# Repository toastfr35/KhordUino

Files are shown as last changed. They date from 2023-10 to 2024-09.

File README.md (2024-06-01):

<p align="center">
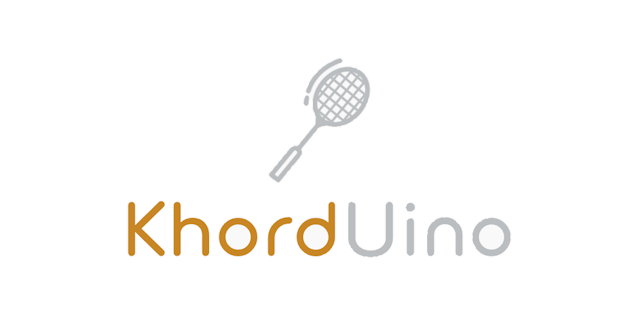
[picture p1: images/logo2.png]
  
</p>

# KhordUino (3D Printed Electronic Badminton Stringer)

Welcome to the KhordUino project, a 3D Printed Electronic Badminton Stringer. 

https://github.com/toastfr35/KhordUino/assets/11369231/e21abeb8-c3cd-45fe-b324-fbe94404d06a

## Mechanical design

A stringing machine usually comprises a stable frame, clamps to hold strings in place and a tensioning system to tighten strings. 
Electronic models have control panels for precision. 

The KhordUino design is quite different from most metal frame stringing machines. In these machines (see below), the rotating joint for the frame is quite far from the tensioning plane.

<p align="center">
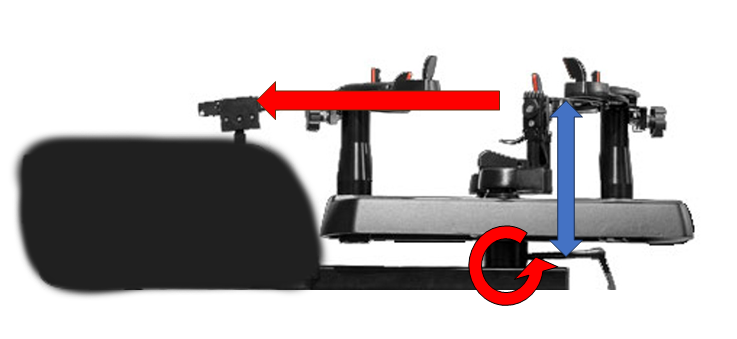
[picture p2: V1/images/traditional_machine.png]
  
</p>

In order to not require many metal components the rotating element (holding the racket) and the part pulling 
on the strings should be aligned as much as possible to minimise the moment (blue arrow).
This is achieved by keeping the machine quite flat (which is also great for storage).

<p align="center">
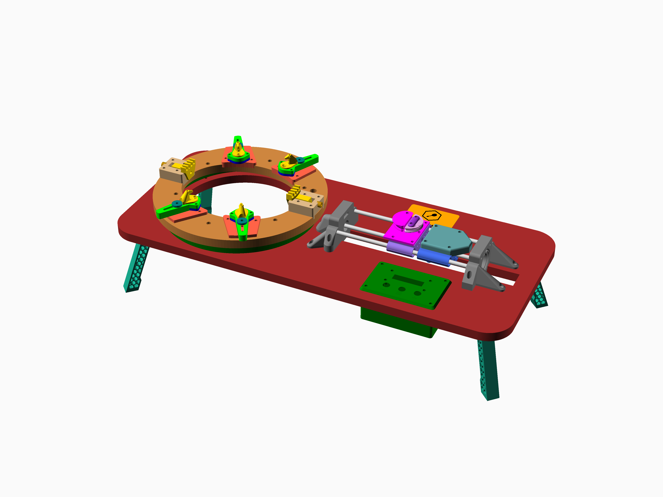
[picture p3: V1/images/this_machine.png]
  
</p>

<p align="center">
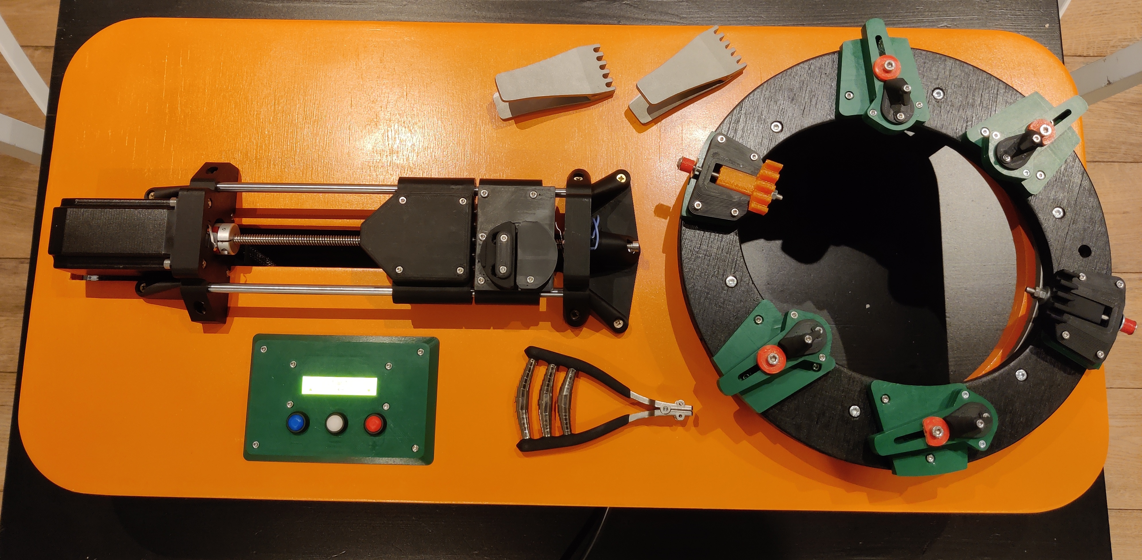
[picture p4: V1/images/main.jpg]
  
</p>

The rotation joint is kept very close to the racket face. This can only be achieved by using a large bearing "around" the racket rather than underneath it.
As the rotating joint and the tensioning part of the machine are almost in the same plane the resulting Moment is greatly reduced.

## BOM

[KhordUino Bill of Material (spreadsheet)](https://docs.google.com/spreadsheets/d/1VggcFAZ6FdfzaC9WXAd_AR7_Q7eQJJpP21XG0TGiltw/edit?usp=sharing)

## Documentation

The [Assembly Manual](V1/KhordUino_Manual.pdf) provides a step-by-step guide to print and assemble your own KhordUino.

## License

KhordUino © 2023 by Antoine Colin is licensed under CC BY-NC-SA 4.0

## Versions

KhordUino V1 is available now.

KhordUino V2 is a work in progress and will be made available once fully tested.

## Videos

[Calibration procedure](https://youtu.be/ICjtoKouB5M)

[Using the string puller](https://youtu.be/xCwdWevW81s)

## Updates:

- V1.1 (2024-05-27).  New firmware with easier calibration procedure.

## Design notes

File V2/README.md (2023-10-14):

# Khorduino V2

## Goals

- Lower BOM cost.
- Fewer different parts to assemble.
- Use standard (still cheap) load cell.
- Easier wiring.
- Lighter, smaller.
- Simplified stringing operation.

## Difference with V1

- More compact (base board length and width reduced to minimum).
- Fewer (larger) 3D printed parts.
- Fewer bolts and nuts
- Fewer different sizes of bolts and nuts.
- No linear bearings.
- Different load cell (and placement of).
- Battery powered (via adapters, e.g. Ryobi 18V battery).
- Single limit switch (other limit enforced in software).
- A single 3 positions switch for stringing operation (pull, idle, release).
- No LCD. Instead Bluetooth + Android/IOS App for settings.
- Slightly longer legs for a bit more clearance.
- Buzzer to indicate desired tension is reached.

## What will be the same

The general design remains the same.

- NEMA23 stepper motor (required for the needed torque).
- Large bearing to access the racquet face from top and bottom.

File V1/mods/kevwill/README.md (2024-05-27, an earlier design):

[kevwill Khorduino Remix](https://www.thingiverse.com/thing:6637585)

#### Summary

I remixed a few parts from toastfr35's KhordUino badminton stringing machine to fit my specific needs:

1.  PSU Box 1 (PSU_Box_1) and Box 2 (PSU_Box_2): I added a cutout for a C13 socket and switch, and modified the vent holes to fit my PSU.
2.  Control Panel Body (CP_body): I modified the external holes to accommodate my wiring and changed the interior mounting posts to fit the Arduino Nano breakout board, buck converter, and terminal block that I used in my build.
3.  Working disc base segment (WD_base_segment): I combined two working disc base segments into one piece to make assembly easier.
4.  Tool drawer (Drawer) and rail (Drawer_rail): I modified the drawer and rail so that the drawer latches closed, preventing the drawer from sliding open and spilling tools during transport.

Here are the specific parts I ordered that fit these modifications:

[https://www.amazon.com/gp/product/B06XK2ZNKC/ref=ppx_yo_dt_b_search_asin_title?ie=UTF8&psc=1](https://www.amazon.com/gp/product/B06XK2ZNKC/ref=ppx_yo_dt_b_search_asin_title?ie=UTF8&psc=1)  
[https://www.amazon.com/gp/product/B09LGX9MQX/ref=ppx_yo_dt_b_search_asin_title?ie=UTF8&psc=1](https://www.amazon.com/gp/product/B09LGX9MQX/ref=ppx_yo_dt_b_search_asin_title?ie=UTF8&psc=1)  
[https://www.amazon.com/gp/product/B0BF9H89HD/ref=ppx_yo_dt_b_search_asin_title?ie=UTF8&psc=1](https://www.amazon.com/gp/product/B0BF9H89HD/ref=ppx_yo_dt_b_search_asin_title?ie=UTF8&psc=1)  
[https://www.amazon.com/gp/product/B0BXKZQB1H/ref=ppx_yo_dt_b_search_asin_title?ie=UTF8&psc=1](https://www.amazon.com/gp/product/B0BXKZQB1H/ref=ppx_yo_dt_b_search_asin_title?ie=UTF8&psc=1)  
[https://www.amazon.com/dp/B0BMTKGCM6?psc=1&ref=ppx_yo2ov_dt_b_product_details](https://www.amazon.com/dp/B0BMTKGCM6?psc=1&ref=ppx_yo2ov_dt_b_product_details)  
[https://www.amazon.com/gp/product/B085CGGH4W/ref=ppx_yo_dt_b_search_asin_title?ie=UTF8&psc=1](https://www.amazon.com/gp/product/B085CGGH4W/ref=ppx_yo_dt_b_search_asin_title?ie=UTF8&psc=1)

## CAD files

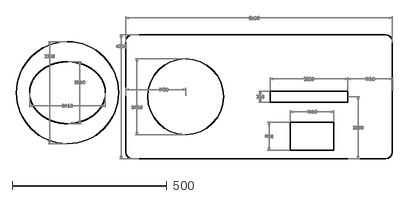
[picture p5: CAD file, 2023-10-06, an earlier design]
V1/plywood_template/board.dxf
1215.3 x 459.3

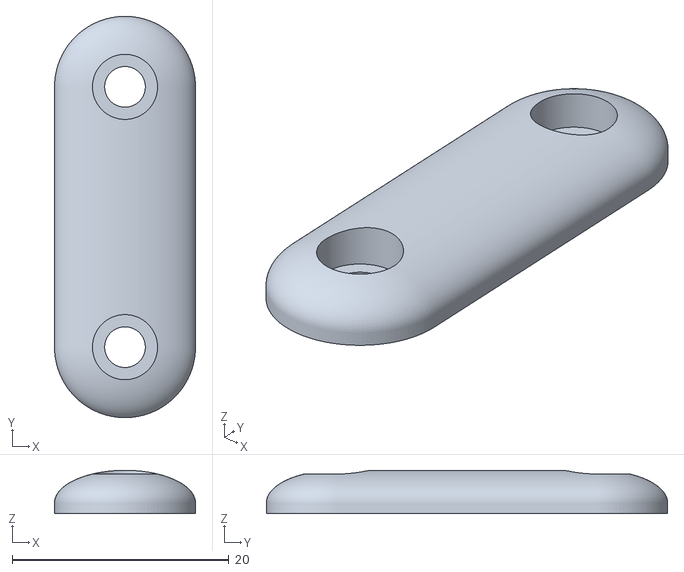
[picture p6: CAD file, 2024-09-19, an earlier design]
V1/STLs/GS_mobile_jaw_retainer.stl
13.0 x 37.0 x 4.00

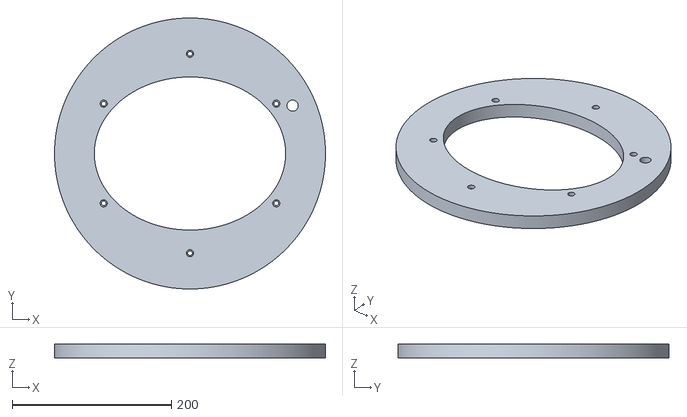
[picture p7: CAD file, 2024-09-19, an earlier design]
V1/STLs/WD.stl
340.0 x 340.0 x 18.0

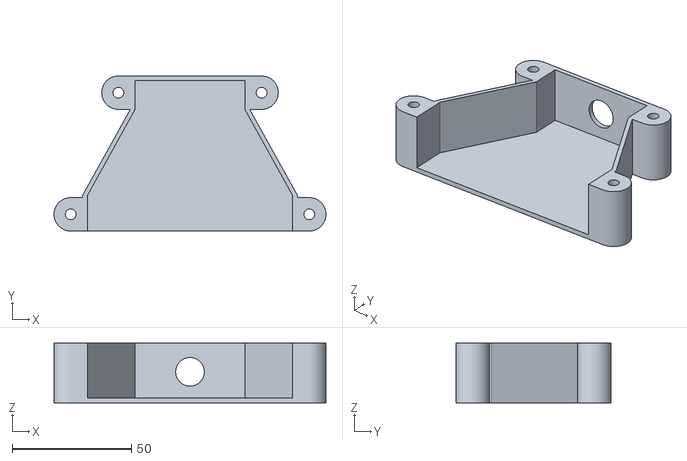
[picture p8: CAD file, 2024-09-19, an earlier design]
V1/STLs/BB_stepper_driver_cover.stl
114.0 x 65.0 x 25.0

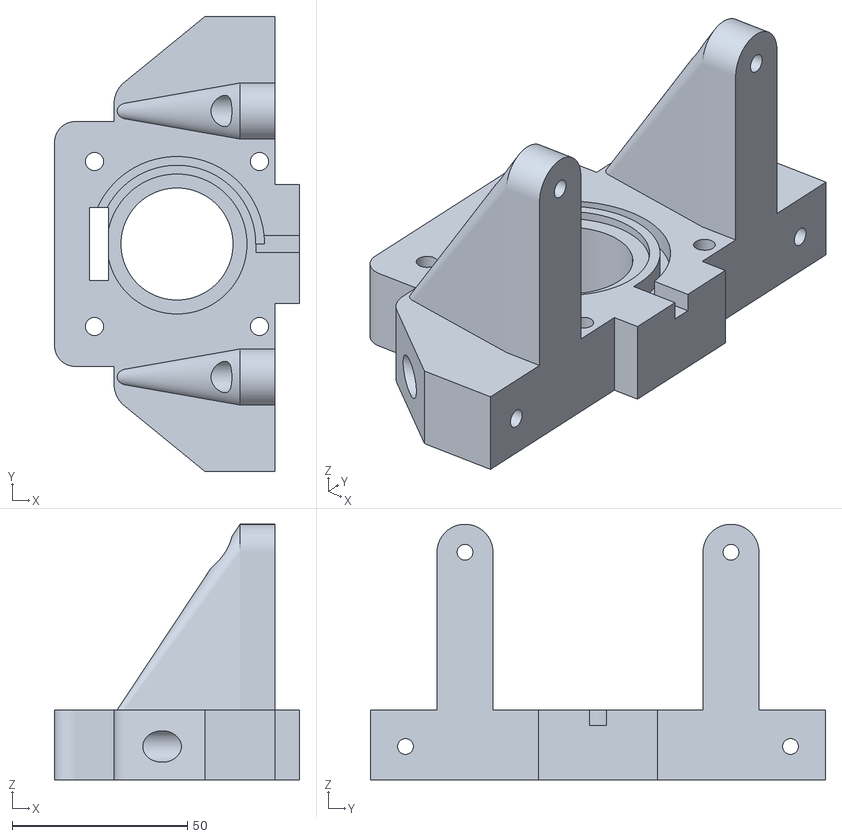
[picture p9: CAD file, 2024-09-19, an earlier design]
V1/STLs/MB.stl
70.0 x 130.0 x 73.0

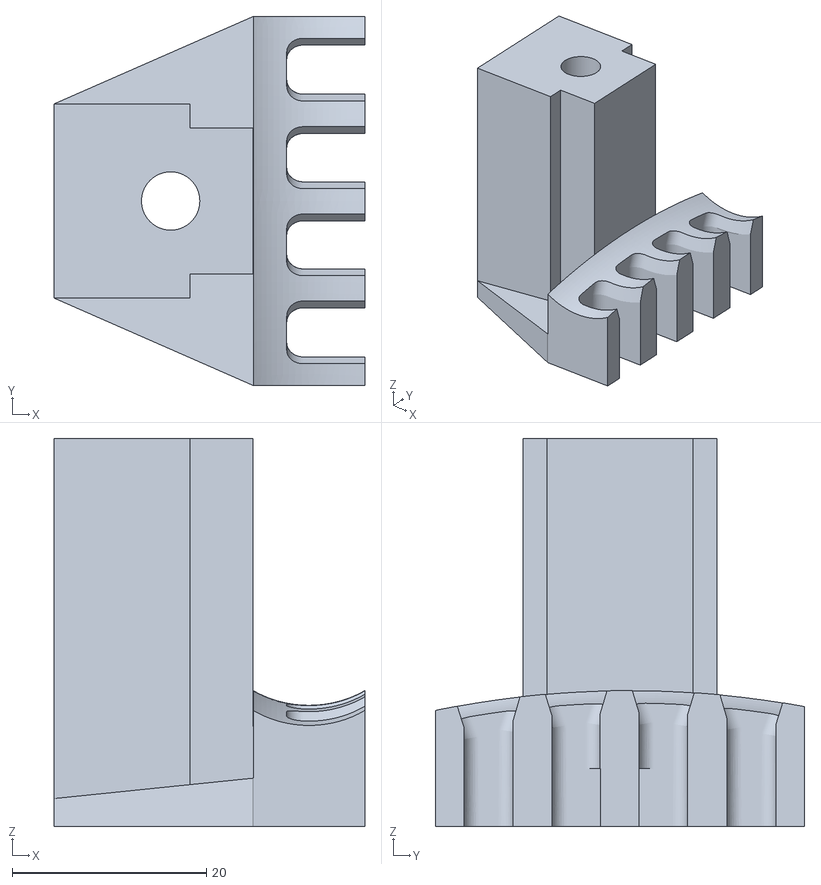
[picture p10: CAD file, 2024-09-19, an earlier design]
V1/STLs/THS_gripper.stl
32.0 x 38.0 x 40.0

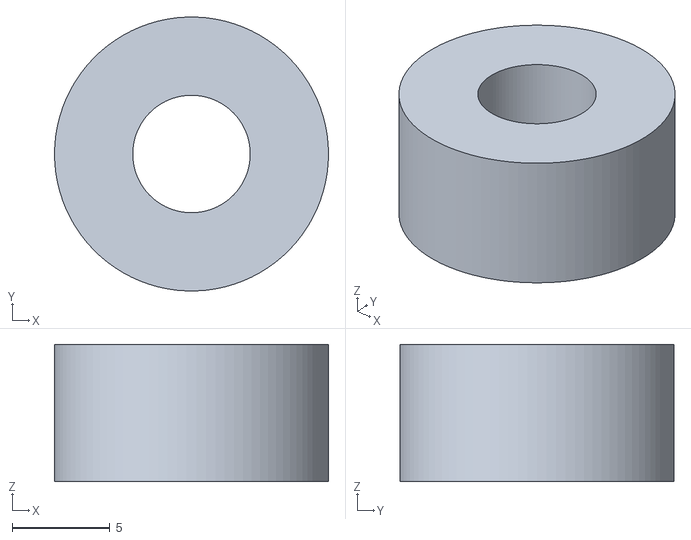
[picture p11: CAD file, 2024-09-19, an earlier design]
V1/STLs/WD_spacer.stl
14.0 x 14.0 x 7.00

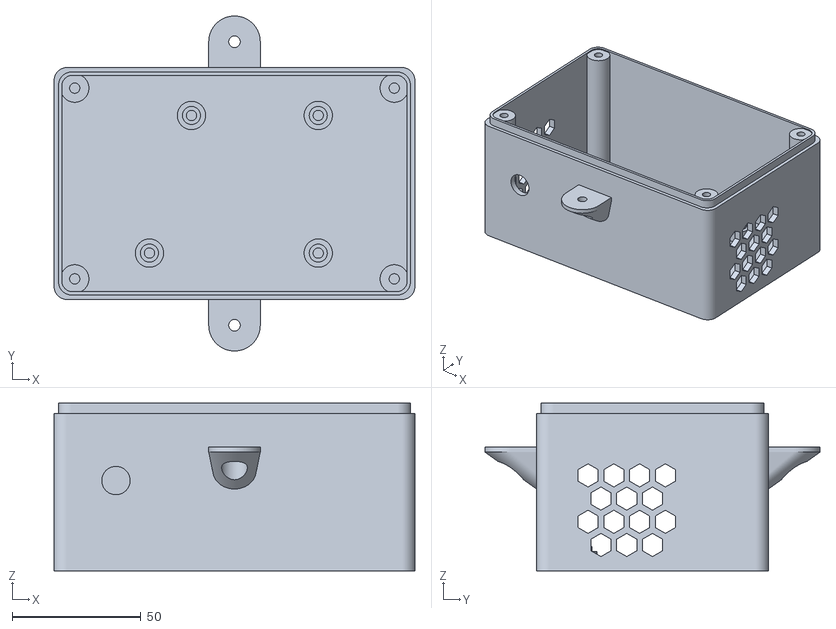
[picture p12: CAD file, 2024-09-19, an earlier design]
V1/STLs/CP_body.stl
140.0 x 130.0 x 65.0

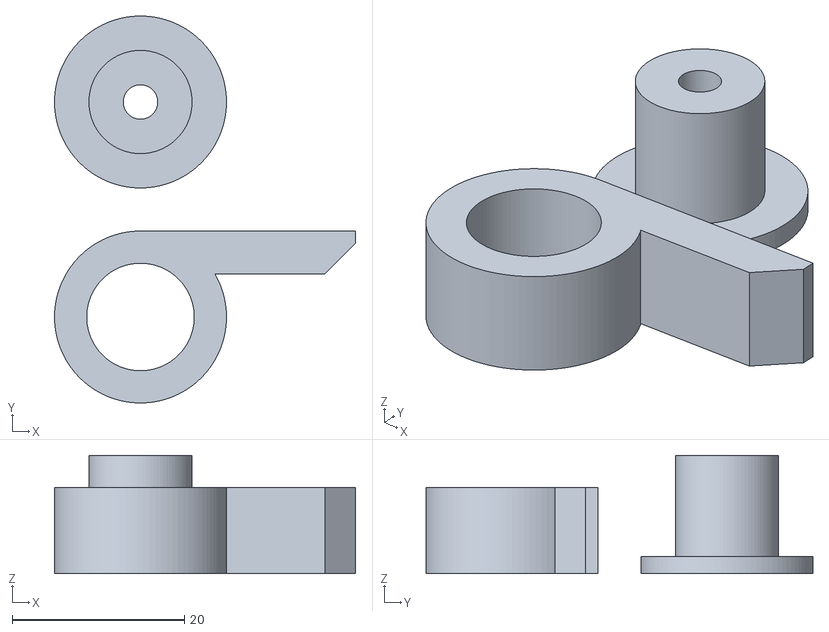
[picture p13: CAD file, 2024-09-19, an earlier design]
V1/STLs/Drawer_latch.stl
35.0 x 45.0 x 13.8

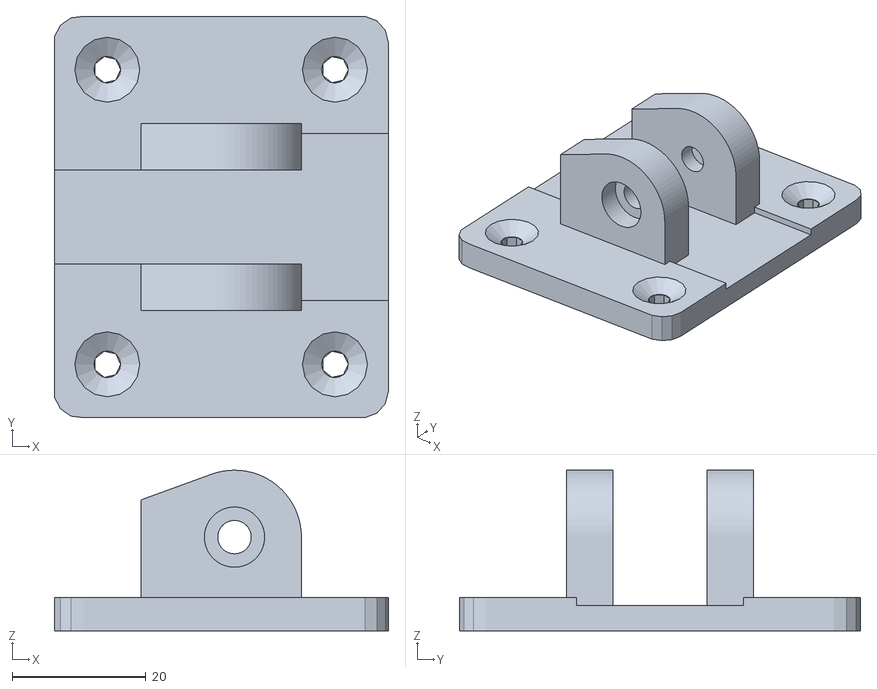
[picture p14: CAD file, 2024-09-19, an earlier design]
V1/STLs/BB_leg_hinge.stl
49.9 x 59.9 x 24.0

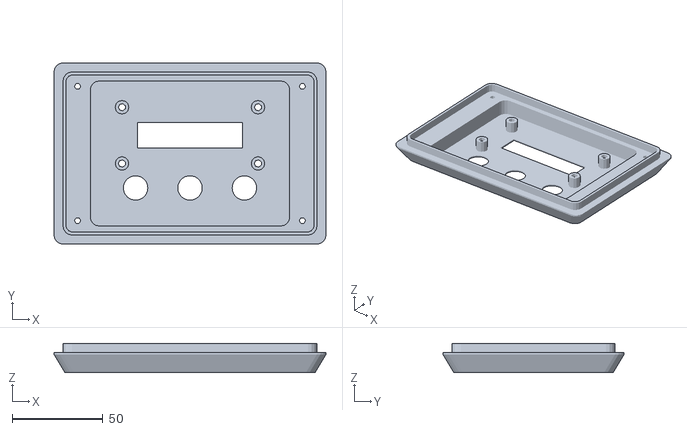
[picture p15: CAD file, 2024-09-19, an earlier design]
V1/STLs/CP_cover.stl
150.0 x 100.0 x 16.0

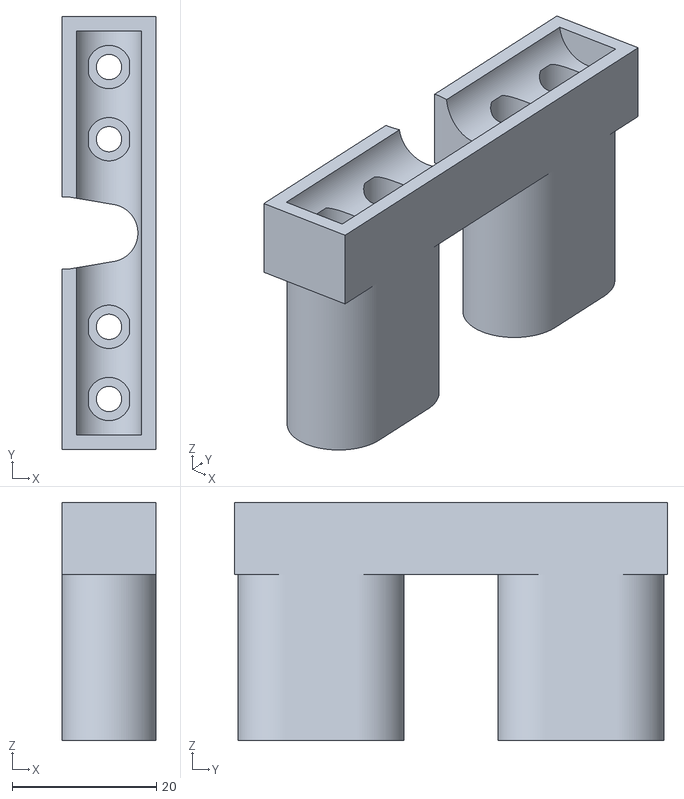
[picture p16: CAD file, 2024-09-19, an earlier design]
V1/STLs/GS_springs_housing.stl
13.0 x 60.0 x 33.0

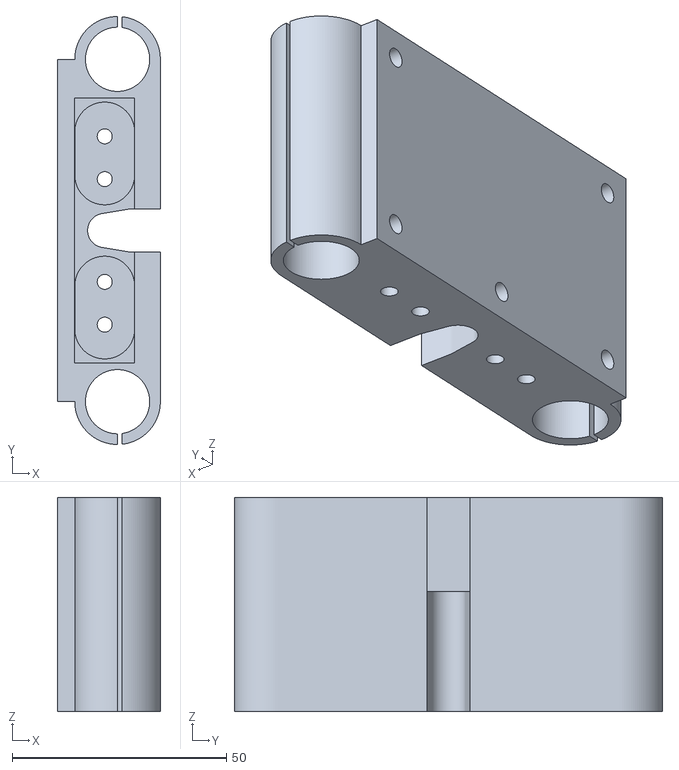
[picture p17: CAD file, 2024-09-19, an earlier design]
V1/STLs/GS_body.stl
24.0 x 100.0 x 50.0

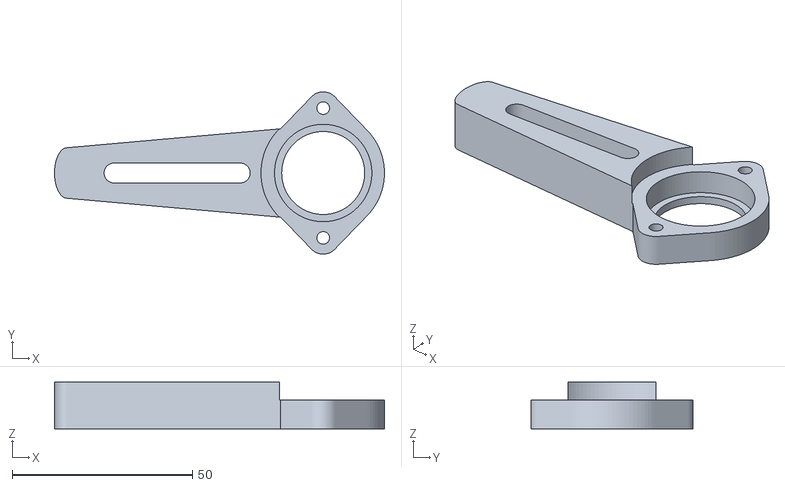
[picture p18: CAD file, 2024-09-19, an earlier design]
V1/STLs/RFS_arm.stl
91.5 x 45.0 x 13.0

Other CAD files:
V1/STLs/BB.stl
V1/STLs/Drawer_rail.stl
V1/STLs/EB.stl
V1/STLs/THS_spacer.stl
V1/SCADs/BB_leg.scad
V1/SCADs/BB_leg_hinge.scad
V1/SCADs/BB_stepper_driver_bracket.scad
V1/SCADs/BB_stepper_driver_cover.scad
V1/SCADs/BB.scad
V1/SCADs/BB_cable_retainers.scad
V1/SCADs/CP_body.scad
V1/SCADs/CP_cover.scad
V1/SCADs/Drawer.scad
V1/SCADs/Drawer_latch.scad
V1/SCADs/Drawer_rail.scad
V1/SCADs/EB.scad
V1/SCADs/GS_body.scad
V1/SCADs/GS_fixed_jaw.scad
V1/SCADs/GS_mobile_jaw.scad
V1/SCADs/GS_mobile_jaw_retainer.scad
V1/SCADs/GS_springs_housing.scad
V1/SCADs/MB.scad
V1/SCADs/PSU_box_1.scad
V1/SCADs/PSU_box_2.scad
V1/SCADs/RFS_arm.scad
V1/SCADs/RFS_base.scad
V1/SCADs/RFS_bottom_cap.scad
V1/SCADs/RFS_gripper.scad
V1/SCADs/RFS_rotating_disc.scad
V1/SCADs/RFS_washer.scad
V1/SCADs/THS_base.scad
V1/SCADs/THS_body.scad
V1/SCADs/THS_gripper.scad
V1/SCADs/THS_spacer.scad
V1/SCADs/TS_body.scad
V1/SCADs/TS_top.scad
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

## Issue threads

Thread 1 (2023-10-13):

CAD files

drnedm, 2023-10-13:
Hi,
thanks so much for sharing this project! I'm building the tensioner part to use it on an old existing drop-weight machine. In order to make an adapter plate, it would be super helpful to not only have the STLs but also an assembled CAD file, STEP format or similar.
Would you be willing to share that as well?

Cheers,
D

toastfr35, 2023-10-13:
Hi, the source is all OpenSCAD but the code is quite a mess at the moment. Let me know which STLs you need and I'll clean these first and put them online.

drnedm, 2023-10-13:
Great, thanks again!

openSCAD is also perfectly fine, I'd be fine with messy openSCAD as well.

For me personally the whole tensioner assembly is relevant, while the rotating racket mount part is not.

drnedm, 2023-10-13:
So from the manual I think that would be

EB.stl
MB.stl
TS_body.stl
TS_top.stl
GS_body.stl
GS_springs_housing.stl
GS_fixed_jaw.stl
GS_mobile_jaw.stl
GS_mobile_jaw_retainer.stl

toastfr35, 2023-10-13:
Here they are in the SCADs directory.  Not super-clean but I'll improve this later.

Closed 2023-10-13.

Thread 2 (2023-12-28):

Load cell and motor firmware

Phyntox, 2023-12-28:
Hi. I have a problem getting the readings from the load cell. I think I connected everithing right.
Also, I have problems running the motor. Nothing seems to happen.

I am using the Arduino UNO. Maybe this is the problem. All the buttons are working.

Could you please share the wiring diagram (more detailed like the DM542 wiring..)

Also it would be nice to have a cancle or back button when you are in the set and pull option.

And a reset button maybe  (Maybe combination of long press of two buttons)?

klwill1192, 2023-12-30:
Can you tell me which luggage scale you bought to get the load cell?  I've bought a couple and neither was the right one for this project.  Thank you.

Phyntox, 2023-12-30:
Any load cell should work, but i thik the problem is that the code is tailored to one type. I'm tearing the code back to the raw reading of the cell and I'll try to "calibrate" the reading to get something useful out

Phyntox, 2023-12-30:
I think i somehow calibrated the load cell inside the code.

Now i just need to see the actual wiring of the DM542. Can someone share a diagram or picture?

klwill1192, 2023-12-31:
I'm still a little ways away from wiring up the badminton stringer, but
here are some pics from another project I designed that also used a DM542
and stepper motor.  You can see how the stepper motor connects to the DM542
here.  If the motor spins the reverse of what you expect, I believe
swapping the two inner or two outer wires will fix the problem.

Here is the original project:  https://imgur.com/gallery/xcwB9ku

[image: IMG_20231230_201622__01.jpg]
[image: IMG_20231230_201440__01.jpg][image: IMG_20231230_201528__01.jpg]

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

klwill1192, 2023-12-31:
> I think i somehow calibrated the load cell inside the code.
>
> Now i just need to see the actual wiring of the DM542. Can someone share a diagram or picture?

I'm still a little ways away from wiring up the badminton stringer, but
here are some pics from another project I designed that also used a DM542
and stepper motor.  You can see how the stepper motor connects to the DM542
here.  If the motor spins the reverse of what you expect, I believe
swapping the two inner or two outer wires will fix the problem.

Here is the original project:  https://imgur.com/gallery/xcwB9ku

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

Phyntox, 2023-12-31:
I did it. i forgot to wire the GNDto EN-. now it works. I need to fine tune the pulling force.

StealthSZN, 2024-01-03:
Hello,

I'm new to the 3d print world, and going to attempt this project. Do you guys have any additional recourses/photos/videos that you could share, and would help me out. Reading over the manual, it would be great to have some videos or pictures to go along as I on not to well versed in these types of projects.

I would appreciate it a ton!

StealthSZN, 2024-01-03:
It would also be great if someone could look over my parts list to make sure everything I am going to order is compatible.

Phyntox, 2024-01-03:
Buy as it is written in BOM. but expect to do some 3d modelling. My cell was different so i had to make an adapter. And then the calibration of the cell.  And steeper driver... just start and learn and solve problems when they occur. Ill try to help as much as i can 😉

StealthSZN, 2024-01-03:
That would be awesome, only questions I have right now is: do i need an Arduino Breakout board? or do I only need the nano?
and can you link me the lazy susan you used? I cant seem to find one online that matches the photos in the manual.

Do you have another place I can message you if I have any questions?

Thanks a ton!

Phyntox, 2024-01-04:
I used arduino Uno. With breakout board. It's easier. And I made some adjustments regarding the main board. I am planning to make ot a bit different so for the concept testing i just 3d printed the bearing and used airsoft balls. It works perfectly (for testing at least)

klwill1192, 2024-01-04:
> So doable without the breakout board or should I just get one to make it easier?

Both.  I am using a Nano with the breakout board.  It's pretty cheap compared to the total cost of the project, so I think the convenience is worth the expense.

Here's the lazy susan I ordered:  https://www.amazon.com/gp/product/B07T2D8D71

You'll end up drilling out all12 holes, so it doesn't matter if some of them don't go all the way through.  The important thing is that this one had 6 each on both the inner and outer circles.

You probably won't find the bearing that matches the instructions.  I've ordered 10 different luggage scales and none of them were the right type.  I've got four more on the way, but I'm not hopeful.  Fortunately Amazon lets me return the ones I'm not going to use.  I'm currently deciding between modifying one of the luggage scale load cells or purchasing a 30 kg S-type tension load sensor and building my own rig.  Antoine said that V2 will use a different load cell.  It would be nice if he'd give us a sneak peak.  I've reached out through GitHub, but haven't gotten a response yet.

I have also modifiect the PSU box to use an intgrated plug/switch/fuse.

Antoine also said that he elongated the legs a bit for V2, so I may do that with V1.

One more item on the shopping list:  a cheap racket to test with.  Not going to start out with one of my nicer ones.

StealthSZN, 2024-01-04:
Luckily i have a cheap racket I can use haha.

Thank you for all the info, I really appreciate it!

This is the load cell I was going to order, curious to know if you guys think it'll work: https://shorturl.at/rCEIX

klwill1192, 2024-01-04:
> This is the load cell I was going to order, curious to know if you guys think it'll work: https://shorturl.at/rCEIX

Whether or not it will work depends on what's inside the case.  The issue isn't so much the load cell as the hardware that connects to the two sides, and whether it can be adapted to connect between  the gripper and tensioner.

I'm seriously thinking about abandoning the cheap luggage scales and redesign the parts to use this:  https://www.amazon.com/dp/B0CPDZ7RS6

StealthSZN, 2024-01-04:
hmm yeah I knew it might be an issue. I was debating to either attempt to build it now, or wait for V2. I'm only about halfway done printing all the parts. I would be of no help trying to redesign the tensioning unit, but if you figure out a better way and would be willing to share, that would be amazing.

Phyntox, 2024-01-04:
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

StealthSZN, 2024-01-04:
Looks awesome, how were you able to get it to work? just changing the code?

Can you convert it into lbs?

Phyntox, 2024-01-04:
`/********************************************************/
/*                  TENSION                             */
/********************************************************/

/*********************************
 * Display the current tension immediately
 *********************************/
void show_tension_now()
{
  lcd.setCursor(0, 0);
  ///////lcd.print(loadcell.read()); // for testing the output measurement
  lcd.print("     " + String(tension_kg / 10) + "." + String(tension_kg % 10) + " kg    ");
}
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
Phyntox, 2024-01-04:
yes, it can be converted to lbs.
you should calibrate the cell anyway so the numerical readout doesnt really matter.
And in the code press ctrl+H and replace the kg for lbs... but in my case I converted lbs to kg.

StealthSZN, 2024-01-04:
awesome thank you!

Phyntox, 2024-01-04:
I've made quiet a lot of changes. But making it easy for anyone to calibrate the cell is complex. Doable, but unfortunately not with my low knowledge of the code.

StealthSZN, 2024-01-04:
I have basic understanding of python and some other languages. I've never done anything with arduino.

Is your machine up and running? @Phyntox

Phyntox, 2024-01-04:
Hint: when calibrating, first find the factor that makes all the reading through the tension spectre has the same error. So for example when adjusting to 35 lbs the actual tension mesured with external scale should be 30 and when stringing with 25 the actual 20... after that, you just add or subtract the difference of 5 lbs for example...

StealthSZN, 2024-01-04:
So you're saying in your case it was 5lbs but mine may be different depending on the cell?

Phyntox, 2024-01-04:
Yes I strung one racket at 10 kg, just to proof myself if it is worth developing. Now that i have done that succesfully, I will upgrade the frame gripping mechanism made from some Alu 20x20 profiles. and later I will probbably develope some new string gripping mechanism.
The thing that botheres me the most is the tension check rate, which is causing the stopping of the motor while tensioning.
Increasing it's value, does nothing. the check rate just stays at some frequency, that is either way anoying. and my understanding of the programming is not sufficient for this troubleshooting.
I tried pasting the video with sound but was too big.

Phyntox, 2024-01-04:
> So you're saying in your case it was 5lbs but mine may be different depending on the cell?

Yes in my case the actual reading was 1,1 kg to low, so I adjusted it.

StealthSZN, 2024-01-04:
Hmmm, i might just wait until he releases V2 or until someone creates a design with less room for error.

Thank you both for the info, I may print the rest of the parts and attempt it soon and if I've worked up the courage!

If you have any other way I can contact you let me know, I can give out my instagram or something like that. I'd love to see pictures/videos with it actually stringing a racket!

Phyntox, 2024-01-04:
It's really easy.  Instead of the code that shows the tension on led, you paste only load cell read.  And you go to test and see what values are you getting.. then work from there.

klwill1192, 2024-01-10:
I've decided to go in a slightly different direction from the cheap luggage scales.  I just ordered the 30kg version of this load cell:  https://www.aliexpress.us/item/3256805789835547.html

And a selection of these M6 threaded T handles:  https://www.aliexpress.us/item/3256805500831086.html

I think I'll end up using the M6x25mm and M6x50mm, but I bought several sizes to play it safe.  I've already modeled the GS_springs_housing and TS_body in Fusion, and I'll make the necessary changes to accommodate the load sensor and appropriate T handles once they arrive.

StealthSZN, 2024-01-10:
That's awesome, keep me updated with results!

klwill1192, 2024-01-21:
Along with a dozen scales from Amazon (none of which had the right type of load sensor for this project), I also ordered a few from Temu.  Lo and behold, two of three had the right innards.  Still waiting for my Aliexpress load sensor and threaded T-handles to arrive, but in the meantime I have the right load sensor for the original design to play with--plus a spare, in case anyone is interested.

Phyntox, 2024-01-21:
Again.  Don't go buying the kids cells too cut the code.  Adjust the code and any load cell will work

Phyntox, 2024-01-21:
It's just a matter of calibration

StealthSZN, 2024-01-21:
Nice! Hopefully the rest of the way is smooth sailing. Was it the one you linked earlier?

klwill1192, 2024-01-22:
> Again. Don't go buying the load cells too fit the code. Adjust the code and any load cell will work

I was shopping for load cells to fit the existing 3D-printed hardware.  But before these arrived I had already decided to order a different load cell and hardware.  I'm still waiting for delivery of that other load cell, but I now have something to test with before the new load cell arrives.  Once it does, I'll redesign the 3D-printed parts to fit.

Phyntox, 2024-01-22:
Please let me know if your motor is also stopping while reading the tension.

magoralczyk, 2024-04-08:
Hi, it is a few months later now. How is the development going on version 2? Is there a release on the horizon?

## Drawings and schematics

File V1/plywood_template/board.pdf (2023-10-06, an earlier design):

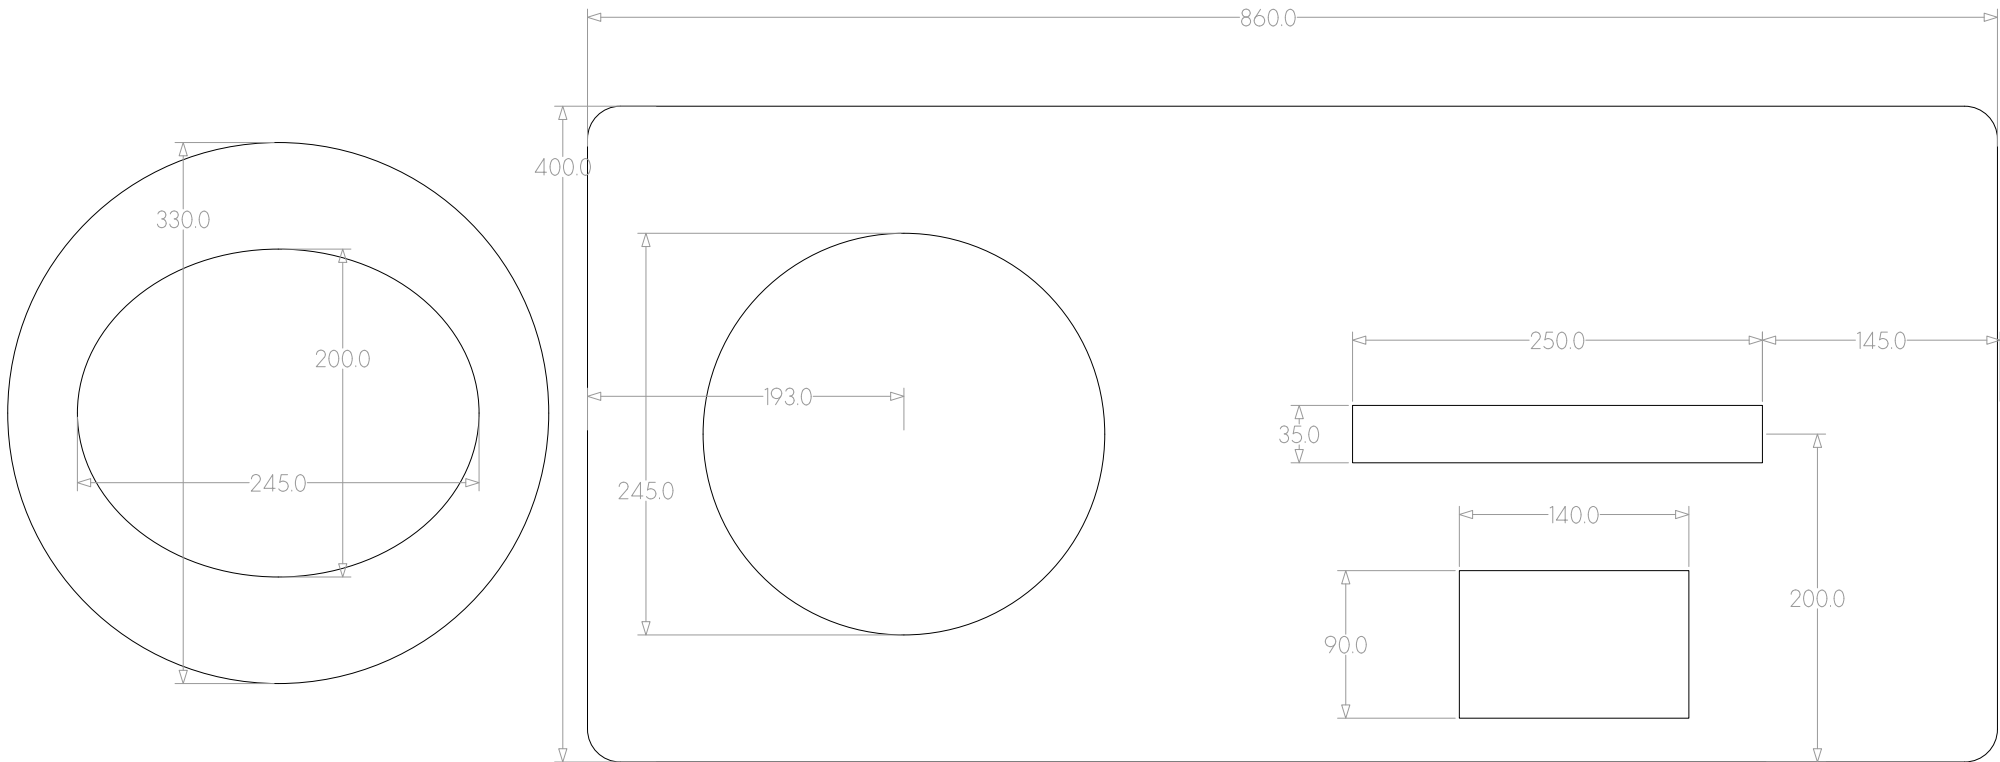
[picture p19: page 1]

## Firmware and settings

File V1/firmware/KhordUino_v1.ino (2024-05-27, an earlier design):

/* Wiring 
    
    Using a CNC shield as breakout board.

    All black wires -> GND


    load cell: (green)  -> (D13)
               (yellow) -> (D12)
               (red)    -> 5V
               
    1 Stepper : pulse+ (green?)  -> (A2) "resume"
                dir+   (violet?) -> (A3) "cool EN"
                enable (orange?) -> (D8) ""
    
    3 buttons:
        (blue)  -> "X-" (D9) & GND
        (white) -> "Y-" (D10) & GND
        (red)   -> "Z-" (D11) & GND

    limit switches
        limit pull (green)  -> "Hold"  (A1)
        limit push (blue)  ->  "Abort" (A0) 
    
    LCD
       SCL (yellow) -> (A5)
       SDA (blue)   -> (A4)
       VCC (red)    -> 5V 

*/
 

/*************************************

START -> 'Ready?' -[any button]-> INIT_POS -> [any button] -> SET_LBS -> [+/-/ok] -> READY  

READY -> [+] -> PULL -> [-] -> RELEASE -> READY
      -> [M] -> SET_LBS -> [+/-/ok] -> READY 

***************************************/


/*********************************/

#define version String("1.1")

#include <Wire.h>
#include <LiquidCrystal_I2C.h>
#include "HX711.h"
#include <EEPROM.h>


// LOAD CELL
#define LOADCELL_DOUT_PIN 13  // green D13
#define LOADCELL_SCK_PIN 12   // yellow D12
HX711 loadcell;
float f_a;
float f_b;

// Stepper
#define EN 8     // stepper motor enable, low level effective
#define X_DIR A3  //X axis, stepper motor direction control
#define X_STP A2  //X axis, stepper motor control
//#define Y_DIR 3  //Y axis, stepper motor direction control
//#define Y_STP 6  //Y axis, stepper motor control

// BUTTONS
#define NB_BUTTONS 5
#define BUTTON_BLUE 0
#define BUTTON_WHITE 1
#define BUTTON_RED 2
#define BUTTON_LIMIT_PULL 3
#define BUTTON_LIMIT_PUSH 4
#define BUTTON_PIN_BLUE 9         // X-stop (green wire)
#define BUTTON_PIN_WHITE 10       // Y-stop (white wire)
#define BUTTON_PIN_RED 11         // Z-stop (brown wire)
#define BUTTON_PIN_LIMIT_PULL A1  // Hold  (blue wire)
#define BUTTON_PIN_LIMIT_PUSH A0  // Abort   (green wire)
int button_pin[NB_BUTTONS] = { BUTTON_PIN_BLUE, BUTTON_PIN_WHITE, BUTTON_PIN_RED, BUTTON_PIN_LIMIT_PULL, BUTTON_PIN_LIMIT_PUSH };
bool button_pressed[NB_BUTTONS] = { false };

// LCD
LiquidCrystal_I2C lcd = LiquidCrystal_I2C(0x27, 16, 2);


/*********************************/
unsigned long tension_int = 0;          // current load cell value
unsigned long tension_lbs = 0;          // current tension in lbs
unsigned int target_tension_lbs = 0;    // tension to achieve
bool tension_display_enabled = false;   // should the current tension be automatically displayed when updated?

bool direction_pull = true;             // which way is it moving?
const unsigned int pull_speed = 100;    // nominal speeds
const unsigned int push_speed = 75;


/*********************************/
//#define debug(X)
void debug(String msg) {Serial.println(msg);}


void stepper_disengage();
void stepper_engage();

void(* resetFunc) (void) = 0;//declare reset function at address 0


/*********************************
 * Initialisation
 *********************************/
void setup_lcd();
void main_menu();

void setup() 
{
  int i;

  Serial.begin(9600);
  Serial.println("Hi");
  Wire.begin();

  // initialize lcd
  setup_lcd();
  lcd.backlight();
  lcd.clear();
  lcd.setCursor(1, 0);
  lcd.print("Khorduino " + version);

  // initialize loadcell
  loadcell.begin(LOADCELL_DOUT_PIN, LOADCELL_SCK_PIN, 64);  // 128
  loadcell.wait_ready();
  loadcell.set_scale();
  loadcell.tare();  //Reset the loadcell to 0

  // initialize stepper
  pinMode(X_DIR, OUTPUT);
  pinMode(X_STP, OUTPUT);
  pinMode(EN, OUTPUT);
  digitalWrite(X_DIR, true);  // set direction to 'pull'
  stepper_disengage();

  // initialize buttons
  for (i = 0; i < NB_BUTTONS; i++) {
    pinMode(button_pin[i], INPUT_PULLUP);
  }

  // read last configured target tension from eprom
  EEPROM.get(0, target_tension_lbs);
  if (target_tension_lbs > 300) {target_tension_lbs = 300; EEPROM.put(0, target_tension_lbs);}
  if (target_tension_lbs < 180) {target_tension_lbs = 180; EEPROM.put(0, target_tension_lbs);}
  EEPROM.get(4, f_a);
  EEPROM.get(8, f_b);

  debug ("target_tension_lbs = " + String (target_tension_lbs));
  debug ("f_a = " + String (f_a));
  debug ("f_b = " + String (f_b));

  delay(1500);

  main_menu(); 

}

/********************************************************/
/*                   MAIN LOOP                          */
/********************************************************/


/* Actions */
int main_menu_input();
int setup_menu_input();
void reset_puller();         // Move the puller to the 'ready' position
void user_set_target_lbs();  // Let the user set the target tension
int wait_for_input();        // wait for the user: 0-> pull, 1 -> set the target.
int do_pull();               // pull the string. Return:  0 -> hold, 1 -> release
int do_hold();               // hold the string. Return: 0 -> pull, 1-> release, 2 -> SET_LBS
void do_release();           // release the tension

void set_coefficient_A();
void load_cell_test();



void loop() 
{
  enum states { RESET,
                SETUP,
                SET_LBS,
                GET_INPUT,
                PULL,
                HOLD,
                RELEASE };
  static states current_state = RESET;
  static states state_after_set_lbs;
  int choice = -1;

  debug("Current State is " + String(current_state));

  tension_display_enabled = false;

  switch (current_state) {
    // perform action for the current state and move to next state

    case RESET:
      lcd.clear();
      reset_puller();
      current_state = SET_LBS;
      state_after_set_lbs = GET_INPUT;
      break;

    case SET_LBS:
      user_set_target_lbs();
      current_state = state_after_set_lbs;
      break;

    case GET_INPUT:
      choice = wait_for_input();
      if (choice == 0) {
        current_state = PULL;
      } else {
        current_state = SET_LBS;
        state_after_set_lbs = GET_INPUT;
      }
      break;

    case PULL:
      choice = do_pull();
      if (choice == 0) {
        current_state = HOLD;
      } else {
        current_state = RELEASE;
      }
      break;

    case HOLD:
      choice = do_hold();
      if (choice == 0) {
        current_state = PULL;
      } else if (choice == 1) {
        current_state = RELEASE;
      } else {
        current_state = SET_LBS;
        state_after_set_lbs = HOLD;
      }
      break;

    case RELEASE:
      do_release();
      current_state = GET_INPUT;
      break;

    default:
      debug("ERROR");
      break;
  }
}


/********************************************************/
/*                  BUTTONS                             */
/********************************************************/

/*********************************
 * update 'buttons' array by reading 
 * change of state of 5 physical buttons
 *********************************/  
void update_buttons() 
{
  static unsigned long last_change[NB_BUTTONS] = { 0 };
  static int buttons[NB_BUTTONS] = { 1 };
  int i;

  for (i = NB_BUTTONS - 1; i >= 0; i--) {
    int v = digitalRead(button_pin[i]);
    if (buttons[i] != v) {
      unsigned long now = millis();
      unsigned long dt = now - last_change[i];
      if (dt > 50) {
        buttons[i] = v;
        button_pressed[i] = (v == 0);
        last_change[i] = now;
        //debug ("B" + String(i) + " v = " + String(v));
        //debug ("B pressed " + String(i) + " changed to " + String(button_pressed[i]));
      }
    }
  }
}

/*********************************
 * is the PULL limit switch depressed?
 *********************************/ 
bool limit_switch_pull() 
{
  return (digitalRead(BUTTON_PIN_LIMIT_PULL) == 0) ? true : false;
}

/*********************************
 * is the PUSH limit switch depressed?
 *********************************/ 
bool limit_switch_push() 
{
  return (digitalRead(BUTTON_PIN_LIMIT_PUSH) == 0) ? true : false;
}


/*********************************
 * Wait for a button input (with optional timeout in ms)
 ********************************/ 
int wait_button_press(unsigned int timeout = 0) 
{
  unsigned long start = millis();
  unsigned int i, result = 0;
  bool prev[NB_BUTTONS];
  update_buttons();
  for (i = 0; i < NB_BUTTONS; i++) prev[i] = button_pressed[i];

  do {
    update_tension();
    update_buttons();
    for (i = 0; i < NB_BUTTONS; i++) {
      if (!prev[i] && button_pressed[i]) result |= (1 << i);
      if (!button_pressed[i]) prev[i] = false;
    }

    if (timeout != 0) {
      if ((millis() - start) >= timeout) {
        return 0;
      }
    }

  } while (!result);
  return result;
}


/********************************************************/
/*                  TENSION                             */
/********************************************************/

/*********************************
 * Display the current tension immediately
 *********************************/ 
void show_tension_now() 
{
  lcd.setCursor(0, 0);
  lcd.print("    " + String(tension_lbs / 10) + "." + String(tension_lbs % 10) + " lbs  ");
  //debug("Tension = " + String(tension_int) + " " + String(tension_lbs / 10) + "." + String(tension_lbs % 10) + " lbs");
}

/*********************************
 * Display the current tension at most every 0.5 s
 *********************************/ 
void show_tension()
{
  static unsigned long last = 0;
  unsigned long now = millis();
  unsigned long dt = now - last;
  if (dt > 500) {
    show_tension_now();
    last = now;
  }
}

/*********************************
 * Convert load cell value to LBS
 *********************************/ 
// 10lbs = f_a * load_cell + f_y
unsigned long int_to_lbs(unsigned int v)
{
  // lbs = (v - b) / a
  int r;
  float f_v = (float)v;
  r = (int)(10.0 * ((f_a * f_v) + f_b));
  if (r < 0) r = 0;
  return r;
}

/*********************************
 * Read load cell and update current tension
 *********************************/ 
void update_tension() 
{
  long v;
  if (loadcell.is_ready()) {
    v = 64 + (loadcell.read() / 1000);
    if (v < 0) v = 0;
    tension_int = v;
    tension_lbs = int_to_lbs(v);
    if (tension_display_enabled) show_tension();
  }
}



/********************************************************/
/*                  MOTORS CONTROL                      */
/********************************************************/

/*********************************
 * Disengage stepper motor
 *********************************/ 
void stepper_disengage() 
{
  digitalWrite(EN, HIGH);
}

/*********************************
 * Engage stepper motor
 *********************************/ 
void stepper_engage() 
{
  digitalWrite(EN, LOW);
}

/*********************************
 * Set stepper to move in PULL direction
 *********************************/ 
void set_direction_pull() {
  if (!direction_pull) {
    direction_pull = true;
    digitalWrite(X_DIR, false);
  }
}

/*********************************
 * Set stepper to move in PUSH direction
 *********************************/ 
void set_direction_push() {
  if (direction_pull) {
    direction_pull = false;
    digitalWrite(X_DIR, true);
  }
}

/*********************************
 * Move the stepper motor one step
 * return 0 if successfull
 *        1 if stop_on_tension is true and the requested tension is reached
 *        2 if the pull limit is reached
 *        3 if the push limit is reached
 *********************************/ 
int motors_one_step(int step_sleep, bool stop_on_tension) 
{
  static unsigned int step_count = 0;
  static unsigned int tension_check_rate = 256;
  static bool tick = false;
  unsigned long start = micros();
  unsigned long now, delta;
  unsigned int sleep = step_sleep;

  tick = !tick;

  if (direction_pull) {

    if (stop_on_tension) 
    {
      // regular (adaptative) check of the tension to see if we should stop
      step_count++;
      if (((step_count % tension_check_rate )== 0)) update_tension();
      if (tension_lbs >= target_tension_lbs) {
        debug("Tension reached");
        return 1;
      }

      // adapt tension check frequency to proximity of target tension
      tension_check_rate = 16;
      if ((target_tension_lbs - tension_lbs) > 50)  {tension_check_rate = 32;}
      if ((target_tension_lbs - tension_lbs) > 100) {tension_check_rate = 1024;}
      if ((target_tension_lbs - tension_lbs) > 200) {tension_check_rate = 8192;}
      
      // Slow down when getting close
      if ((target_tension_lbs - tension_lbs) < 50)  {sleep *= 4;}
      if ((target_tension_lbs - tension_lbs) < 100) {sleep *= 2;}    
    }

    if (limit_switch_pull()) {
      return 2;
    }

  } else {
    if (limit_switch_push()) {
      return 3;
    }
  }

  // adaptive delay 
  now = micros();
  if (now < start) {
    // wrap around
    delayMicroseconds(sleep);
  } else {
    delta = now - start;
    if (delta < sleep) delayMicroseconds(sleep - delta);
  }

  // step
  if (tick) {
    digitalWrite(X_STP, HIGH);
  } else {
    digitalWrite(X_STP, LOW);
  }

  return 0;
}

/*********************************
 * Move the stepper motor n steps in the current direction
 * returns 0 if successfull
 *        1 if stop_on_tension is true and the requested tension is reached
 *        2 if the pull limit is reached
 *        3 if the push limit is reached
 *********************************/
int motors_n_steps(int nb_steps, int step_sleep, bool stop_on_tension) 
{
  unsigned int i, error;
  unsigned int max = 2 * nb_steps;
  unsigned int increment = 1;

  if (nb_steps == 0) {
    // infinite loop
    max = 1;
    increment = 0;
  }

  for (i = 0; i < max; i += increment) {
    error = motors_one_step(step_sleep, stop_on_tension);
    if (error != 0) {
      debug("Stop motors " + String(error));
      update_buttons();
      return error;
    }
  }
  update_buttons();
  return 0;
}



/********************************************************/
/*                    ACTIONS                           */
/********************************************************/

/*********************************
 * Move the puller to the 'ready' position
 *********************************/
void reset_puller() 
{
  int error;

  debug("Reset puller");
  lcd.clear();
  lcd.setCursor(0, 0);
  lcd.print("Wait...");
  stepper_engage();
  set_direction_push();
  motors_n_steps(0, push_speed, false);
  set_direction_pull();
  motors_n_steps(1600, push_speed, false);
  stepper_disengage();
}

/*********************************
 * Let the user set the target tension
 *********************************/
void user_set_target_lbs() 
{
  unsigned int new_target_tension_lbs = target_tension_lbs;
  debug("Set Lbs");
  lcd.clear();
  lcd.setCursor(2, 1);
  lcd.print("-    OK    +");
  while (1) {
    String lbs_str1 = String(new_target_tension_lbs / 10);
    String lbs_str2 = String(new_target_tension_lbs % 10);
    lcd.setCursor(4, 0);
    lcd.print(lbs_str1 + "." + lbs_str2 + " lbs");
    unsigned int button = wait_button_press();
    if (button & (1 << BUTTON_BLUE)) new_target_tension_lbs -= 5;
    if (button & (1 << BUTTON_RED)) new_target_tension_lbs += 5;
    if (new_target_tension_lbs >= 300) new_target_tension_lbs = 300;
    if (new_target_tension_lbs <= 180) new_target_tension_lbs = 180;
    if (button & (1 << BUTTON_WHITE)) break;
  }

  if (new_target_tension_lbs != target_tension_lbs) {
    target_tension_lbs = new_target_tension_lbs;
    unsigned int v;
    EEPROM.get(0, v);
    if (v != target_tension_lbs) EEPROM.put(0, target_tension_lbs);
  }
}

/*********************************
 * Wait for the user: 0-> pull, 1 -> set the target.
 *********************************/
int wait_for_input() 
{
  debug("Wait input");
  lcd.clear();
  lcd.setCursor(0, 0);
  lcd.print("Ready...");
  lcd.setCursor(0, 1);
  lcd.print("      SET   PULL");
  while (1) {
    unsigned int button = wait_button_press();
    if (button & (1 << BUTTON_WHITE)) return 1;
    if (button & (1 << BUTTON_RED)) return 0;
  }
}

/*********************************
 * Pull the string. Return:  0 -> hold, 1 -> release
 *********************************/
int do_pull() 
{
  debug("Do pull");
  lcd.clear();
  lcd.setCursor(0, 1);
  lcd.print("Pulling...");
  tension_display_enabled = true;
  stepper_engage();
  set_direction_pull();
  motors_n_steps(0, pull_speed, true);
}

/*********************************
 * Hold the string. Return: 0 -> pull, 1-> release, 2 -> SET_LBS
 *********************************/
int do_hold() 
{
  debug("Do hold");
  lcd.clear();
  lcd.setCursor(0, 1);
  lcd.print("FREE  SET   PULL");
  tension_display_enabled = true;
  while (1) {
    unsigned int button = wait_button_press(100);
    if (button & (1 << BUTTON_BLUE)) return 1;
    if (button & (1 << BUTTON_WHITE)) return 2;
    if (button & (1 << BUTTON_RED)) return 0;

    if (!limit_switch_pull()) {
      if (tension_lbs < target_tension_lbs) motors_n_steps(32, pull_speed*2, true);
    }
  }
}

/*********************************
 * Release the tension
 *********************************/
void do_release() 
{
  debug("Do release");
  lcd.clear();
  lcd.setCursor(0, 0);
  lcd.print("Releasing...");
  stepper_engage();
  set_direction_push();
  motors_n_steps(0, push_speed, false);
  stepper_disengage();
  delay(3000);
  stepper_engage();
  set_direction_pull();
  motors_n_steps(1600, push_speed, false);
  stepper_disengage();
}



/********************************************************/
/*                                                      */
/********************************************************/

void show_version()
{
  lcd.clear();
  lcd.setCursor(0,0); 
  lcd.print (" Version " + version);
  delay (3000);
}


void show_eeprom()
{
  unsigned int v1;
  float v2;
  EEPROM.get(0, v1);
  lcd.clear(); lcd.setCursor(0,0); lcd.print ("tgt lbs = " + String (v1));
  delay (1000);

  EEPROM.get(4, v2);
  lcd.clear(); lcd.setCursor(0,0); lcd.print ("f_a = " + String (v2));
  delay (1000);

  EEPROM.get(8, v2);
  lcd.clear(); lcd.setCursor(0,0); lcd.print ("f_b = " + String (v2));
  delay (1000);
}


void test()
{
  int button;
  int left = 5;
  lcd.clear();
  lcd.setCursor(left,1); lcd.print("[     ]");  
  tension_display_enabled = 1;
  int done = 0;

  while(done != 0x1F) {
      button = wait_button_press(250);
      update_tension();
      if (button & (1 << BUTTON_BLUE))       {lcd.setCursor(left+1,1); lcd.print("X"); done |= 0x1;}
      if (button & (1 << BUTTON_WHITE))      {lcd.setCursor(left+2,1); lcd.print("X"); done |= 0x2;}
      if (button & (1 << BUTTON_RED))        {lcd.setCursor(left+3,1); lcd.print("X"); done |= 0x4;} 
      if (button & (1 << BUTTON_LIMIT_PULL)) {lcd.setCursor(left+4,1); lcd.print("X"); done |= 0x8;} 
      if (button & (1 << BUTTON_LIMIT_PUSH)) {lcd.setCursor(left+5,1); lcd.print("X"); done |= 0x10;}       
  }
  tension_display_enabled = 0;
  lcd.setCursor(left,1); lcd.print("[@@@@@] OK");  
  delay (3000);
}
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

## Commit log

2023-10-06 1st draft for review
    [BB.stl, BB_cable_retainers.stl, BB_leg.stl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]
2023-10-07 automatic update
    [Drawer.stl, Drawer_rail.stl]
2023-10-13 Removed duplicates
    [BB.stl, BB_cable_retainers.stl, BB_leg.stl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]
2023-10-13 Added some OpenSCAD files.
    [EB.scad, GS_body.scad, GS_fixed_jaw.scad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]
2023-10-14 Moving V1 to sub-directory
    [BB.stl, BB_cable_retainers.stl, BB_leg.stl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]
